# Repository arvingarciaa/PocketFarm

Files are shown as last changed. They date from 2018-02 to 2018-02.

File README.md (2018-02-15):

# PocketFarm

## Abstract

PocketFarm aims to implement precision agriculture on a farm using a network of sensors and data from online weather sources. Low cost and efﬁcient sensors and microcontroller will be used to make an effective farm monitoring system to help the farmer monitor the irrigation. An efﬁcient irrigation system correlates to low cost farming and high yield of crops.

The project is based on a Philippine setting and may include Asia/Philippine-based stores and references.

## Use Case

Since this project is centered around ease of use and convenience, PocketFarm enables a semi-automatic irrigation system through text messaging, weather forecasts, and on-farm sensors. The farmer will have an electronic system integrated directly to their preferred mode of irrigation. Currently, we assume a [gravity irrigation system](https://www.youtube.com/watch?v=6-emq0cxhtU). 



---

## Project Components

### The Farm

To describe some the electronic components, a modified architectural diagram is presented as follows.



To clarify, the electronic system's brain is an [Arduino Uno (clone)](https://www.lazada.com.ph/arduino-uno-r3-arduino-compatible-board-with-usb-13329964.html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), where two sensors--[Capacitive Soil Moisture Sensor](https://www.dfrobot.com/wiki/index.php/Capacitive_Soil_Moisture_Sensor_SKU:SEN0193), and a [DHT22 Temperature and Humidity Module](https://www.dfrobot.com/wiki/index.php/DHT22_Temperature_and_humidity_module_SKU:SEN0137)-- are connected, along with a [solenoid valve](https://www.makerlab-electronics.com/product/plastic-water-solenoid-valve-12v-1-2-nps/) which will control the irrigation system. In addition, a [GSM module](https://www.elecrow.com/sim800c-gprs-gsm-shield-for-arduino.html) serves as the communications link to the central remote server, which does all the processing and decisions.

### The Central Server

The central server is powered by a [Raspberry Pi](https://www.adafruit.com/product/998) hooked to the same [GSM module](https://www.elecrow.com/sim800c-gprs-gsm-shield-for-arduino.html) used in the farm setup. Additionally, the code is written in JavaScript, through Node.js to easily facilitate a front-end solution in the near future.

The server takes in all sensor data from all farm setups (soil moisture, temperature, and humidity), and their corresponding weather forecast data from [WeatherUnderground](https://www.wunderground.com). The server also facilitates scheduled farm irrigation, by sending commands to the farm setups.

---

## What's Inside

The repository contains the following directories.
```bash
./
|-- arduino/  
    # Contains all Arduino-related code, including previous revisions.
|-- server/  
    # Contains all server-related code, including previous revisions. They're meant to be run via Node.js.
|-- schematics/     
    # Contains all PCB schematics and layouts created for both the Raspberry Pi server setup and Arduino setup for the farm.
```

[1]: https://i.imgur.com/4u4o8eJ.png
[2]: https://i.imgur.com/9hq7tE3.png

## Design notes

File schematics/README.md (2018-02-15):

# PCB Fabrication at Home
This is a series of notes for me when I'm fabricating at home, so that I don't make the same mistakes next time. This was originally coming from PocketFarm-related experiences.

All of these are in a Philippine setting, and so will occasionally mention Philippine-based stores and retailers.

---

## Prerequisites
Most of the links here are from online stores, but they're usually _waaay_ cheaper when bought directly in-store (I think it's because the include the shipping costs with the product already, which isn't cost-effective when you're buying a lot from the same store; marketing tactics).
### Basic Stuff (buy and cut the board first!)
* a drill (_I use a Dremel 4000_)
* drill bits (_0.8mm, 1.0mm, 2.5mm, 3.0mm_)
* cut off wheel
* Presensitized PCB (_Kinsten, from e-Gizmo_)
* developer solution (_this came with the Presensitized PCB_)
### Layouting and UV Exposure
* Tracing Paper
* Laser Printer (_Inkjet apparently is equally fine, with a few quirks_)
* DIY UV exposure box (_Diploma Frame, a bunch of UV LEDs, a switch, a DC Jack_)
* Scissors
### Developing and Etching
* Muriatic Acid (_30% Hydrochloric Acid_)
* Hydrogen Peroxide (_Agua Oxigenada, larger volumes might be fine_)
* liquid containers (_I bought a 1L plastic container for the etching solution, and peanut butter jars for the developer solution_)
* two shallow containers for the developer solution and the etching solution
* face mask (_I use both a dust mask and earloop type mask from Mercury Drug_)
* safety goggles
* nitrile gloves (_I bought an industry-grade one for reusability_)
* glass funnel (_cannot emphasize how important this is_)
* nail polish (_acetone_)
* tissue paper (_lots_)
* absorbent cotton
### Placing and Soldering the Components
* soldering iron with a temperature knob (_mine came from China but [this](https://www.lazada.com.ph/adjustable-soldering-iron-60w-yihua-947-iii-8855270.html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) is basically it_)
* soldering [iron tip](https://www.makerlab-electronics.com/product/type-b-soldering-iron-tip/)
* solder (_Super Rubicon, 1 roll, 60%, 1.0m/m_)
* lead free tip tinner (_[Edsyn LT-1](https://www.lazada.com.ph/edsyn-lt-1-lead-free-soldering-tip-tinner-6777194.html), this is to revitalize the soldering tip_)
* blu-tack (_I'm using cheap transparent tape in the meantime._)
* desoldering pump or desoldering wick

---

## PCB Designing and Layouting
I'm using KiCad. I'm swearing by the Getting Started manual. Since I'm only doing single-sided designs, I always use the Back Layer. Here are my Design Rules for Pcbnew.



However, the clearance and the component vias are a bit small. I need to improve on this later.

Place some text on the Back Layer, and make sure it looks inverted. Print it on tracing paper (or transparency film) on a laser printer. When using an Inkjet Printer, make sure that the tracing paper doesn't jam, or curl during the process. Wet ink makes the tracing paper curl, and you may end up with an unusuable print. 

Make sure to inspect the print quality before proceeding.

## Exposing the Photoresist
Place the tracing paper where the printed side faces the PCB later on. You can check if this is the case by looking it through the ceiling, and you can read the text. Tape it into the glass frame, and once done (assuming that the board was already pre-cut), turn off the lights, peel the protective layer, and move quickly.

Place the PCB on the frame, aligned with the printout, lock the frame, and place it on the UV exposure box. Set the timer to 1 minute and 30 seconds, and turn on the lights. While this is happening, wear all protective equipment (goggles, mask, gloves).

## Developing the Exposed Board
The developer solution can be reused. Place caution into dissolving too much into the solution. The middle part of the PCB always develops last, and when this happens too slowly, add a little bit more of the developer powder. Adding too much developer powder will eat out photoresist on areas you don't intend to, and will lead to failure.

Inspect the board visually by rising it from time to time, and make sure you get everything covered (or erased).

## Etching and Exposing the Developed Board
I'm using Cupric Chloride as etchant. Some notes.
* Pure muriatic acid etches very, very quickly. It also produces a lot of fumes, noticeably making it a little bit harder to breathe.
* In the beginning, do a 1:1 ratio of HCl and H2O2.
* Add H2O2 when the solution begins to become olive green in color. Mix well.
* Add HCl when the copper isn't removed quickly. This is usually noticeable at the edges.
* Never add chemicals directly to the board. Do it on the side, then quickly agitate the solution.
* Cupric Chloride on Aqueous Hydrochloric Acid requires reoxidation. If this is done quite frequently, invest on an aquarium air pump (this will also do the agitation necessary for the board), or add H2O2 once in a while.
* CuCl stains. Make sure tissue is in standby nearby. I use a basin below the CuCl container to collect spilling etchant.
* If the recycled etchant doesn't work very well, start with a sizeable amount, then apply more HCl. This allows for a relatively faster etching process, without the excess fumes.
* When satisfied, remove the board from the etchant, dry it with tissue paper, and remove the photoresist with acetone (nail polish). You'd want to use this with cotton balls than tissue paper as cotton holds to the acetone for a little bit longer.
* When all copper components are exposed, clean the board (front and back with alcohol).
* Remember to follow your city guidelines on hazardous waste disposal. Never, ever, try to drain your chemicals directly down the sink!

## Drilling and Cutting the Etched Board
* Dremel 4000's speed works well set to 15--for cutting, drilling, and 5/10 for polishing.
* You'll get a lot of thin drill bits breaking easily, frequently. Make sure to have a lot of backup, and maybe invest on a Multi Chuck (Dremel 4486).
* I'm using a book as a vise/clamp. Invest in a better solution.
* Most through-hole components will work with 0.8mm, but 1.0mm breaks less frequently.
* Big holes are usually of the 3.0mm variant.
* DC jacks use a 2.5mm for the GND and the Switch, and a 3.0mm for the VCC.

## Soldering Through-Hole Components to the PCB
* Use blu-tack for temporarily fastening the components before soldering.
* Make sure to use a sharp tip rather than a tip with a flat end to make soldering jobs less ugly.

---
Take care!

[1]: https://i.imgur.com/gUOFxXU.png

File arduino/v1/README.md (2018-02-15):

# PocketFarm version 1 (Server)

## Setup

The setup for the first revision were as follows.

## The Farm

The farm setup was assigned a GSM number which serves as the main communication point of the farmer. It will react to messages with a specific code/format--get sensor data, get weather forecast, or get irrigation suggestions. To facilitate requests for weather forecasts or irrigiation suggestions, the farm unit will forward the request to the central server, in which it will reply back with the requested resource.

A [GSM shield](https://www.elecrow.com/sim800c-gprs-gsm-shield-for-arduino.html) is attached to the Arduino, with the [Capacitive Soil Moisture Sensor](https://www.dfrobot.com/wiki/index.php/Capacitive_Soil_Moisture_Sensor_SKU:SEN0193) connected to `A5`, and the [DHT22 Temperature and Humidity Module](https://www.dfrobot.com/wiki/index.php/DHT22_Temperature_and_humidity_module_SKU:SEN0137) connected to `A0`.

The code is available at `/arduino/v1/final_working/final_working.ino`.

## The Central Server
The central server relied on an Arduino with a GSM shield to receive texts from the farm units, and a Node.js server to facilitate processing. They are both communicating via WebSockets, and so requires the Arduino connected to both a [GSM shield](https://www.elecrow.com/sim800c-gprs-gsm-shield-for-arduino.html) and an [Ethernet shield](http://www.elecrow.com/w5100-ethernet-shield-for-arduino-p-670.html). 

While this setup offers flexibility (i.e., the Arduino setup can be running 24/7 somewhere connected to a router, and the server can be hosted offshore to ensure reliability), it poses issues on cost, redundancy, and speed.

The Arduino code is available at `/arduino/v1/WebSocketGSMBridge`.
The server code is available at `/server/v1`. It can be run using `npm start`. Make sure to duplicate `/server/v1/example.env` to `/server/v1/.env` and add your keys before running.

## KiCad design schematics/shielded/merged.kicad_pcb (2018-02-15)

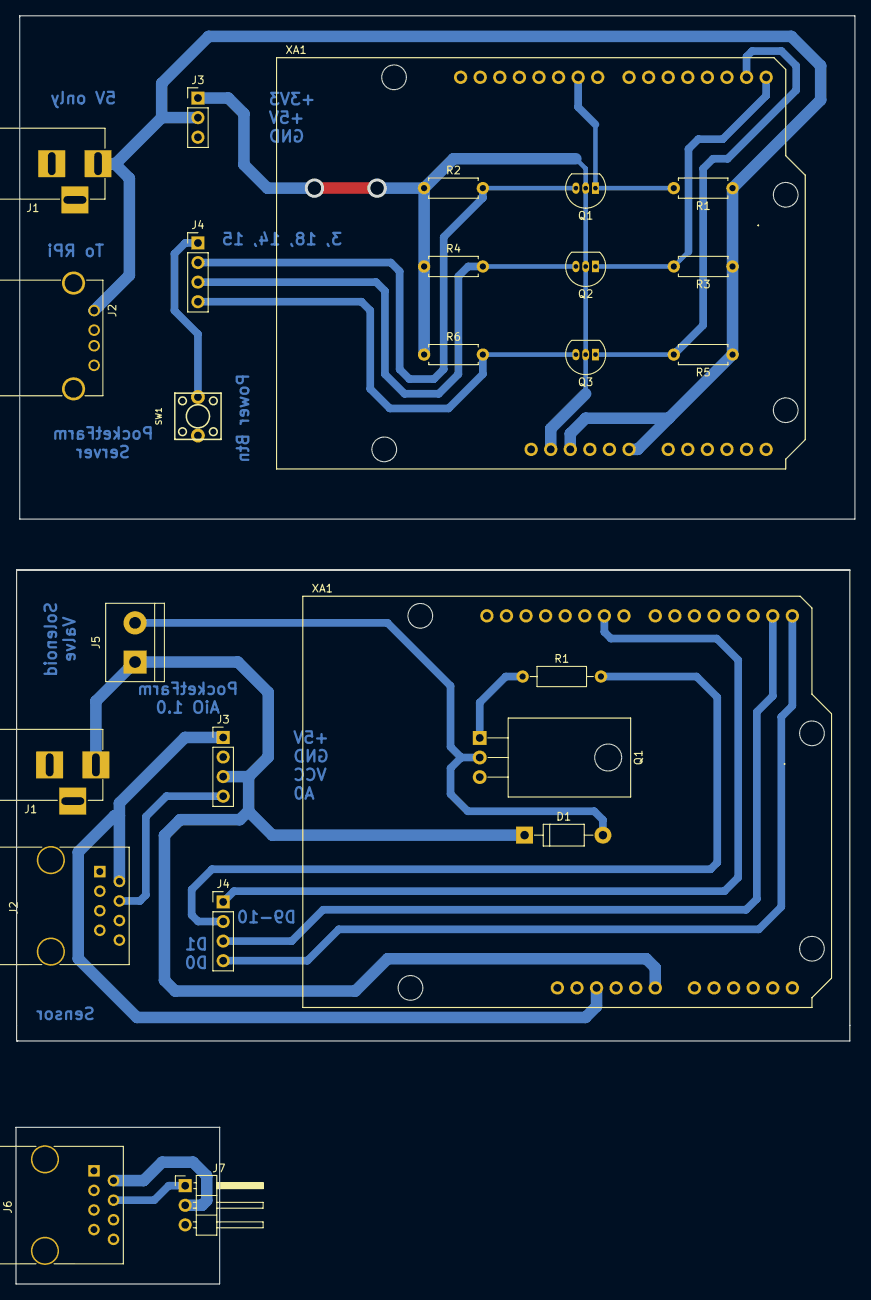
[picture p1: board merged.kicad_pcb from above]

Board: 2 copper layers, 108.8 x 164.5 mm, 26 parts (0 on the bottom side), 37 nets.

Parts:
D1: 1N4001; D_DO-41_SOD81_P10.16mm_Horizontal
J1, J1#2: Jack-DC; BARREL_JACK
J2: USB_A
J2#2: RJ45_BUILTIN; RJ45_8
J3: Conn_01x03_Male; Pin_Header_Straight_1x03_Pitch2.54mm
J3#2, J4, J4#2: Conn_01x04_Male; Pin_Header_Straight_1x04_Pitch2.54mm
J5: Screw_Terminal_01x02; TerminalBlock_bornier-2_P5.08mm
J6: RJ45_SENSOR; RJ45_8
J7: Conn_01x03_Male; Pin_Header_Angled_1x03_Pitch2.54mm
Q1, Q2, Q3: 2N7000; TO-92_Inline_Narrow_Oval
Q1#2: TIP120; TO-220-3_Horizontal
R1, R2, R3, R4, R5, R6: 10k; R_Axial_DIN0207_L6.3mm_D2.5mm_P7.62mm_Horizontal
R1#2: 1k; R_Axial_DIN0207_L6.3mm_D2.5mm_P10.16mm_Horizontal
SW1: SW_SPST; SPST-2-PIN_6mm_thru
XA1, XA1#2: Arduino_Uno_Shield

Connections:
+3V3: J3.1, Q1.2, Q2.2, Q3.2, R2.1, R4.1, R6.1, XA1.3.3V
+5V: J1.1, J2.1, J2#2.2, J3.2, J3#2.1, J6.2, J7.2, R1.1, R3.1, R5.1, XA1.5V1, XA1.VIN, XA1#2.5V1
/A0: J2#2.4, J3#2.4, J6.4, J7.1
/D0_TX1: J4#2.4, XA1#2.D0
/D1_RX1: J4#2.3, XA1#2.D1
/D9: J4#2.1, XA1#2.D9
/D10: J4#2.2, R1#2.2
/GPIO3: J4.1, SW1.1
/GPIO18: J4.2, Q1.3, R2.2
/RXD0_15: J4.4, Q3.3, R6.2
/TXD0_14: J4.3, Q2.3, R4.2
GND: J1.2, J1#2.2, J2.4, J2#2.1, J2#2.3, J2#2.5, J2#2.6, J2#2.7, J2#2.8, J3.3, J3#2.2, J6.1, J6.3, J6.5, J6.6, J6.7, J6.8, J7.3, Q1#2.3, SW1.2, XA1.GND1, XA1.GND2, XA1.GND3, XA1#2.GND1, XA1#2.GND2, XA1#2.GND3
unnamed: D1.2, J5.2, Q1#2.2
unnamed: J1.3, J1#2.3
unnamed: Q1.1, Q1#2.1, R1.2, R1#2.1, XA1.D9
unnamed: Q2.1, R3.2, XA1.D0
unnamed: Q3.1, R5.2, XA1.D1
unnamed: XA1.A0, XA1#2.A0
unnamed: XA1.A1, XA1#2.A1
unnamed: XA1.A2, XA1#2.A2
unnamed: XA1.A3, XA1#2.A3
unnamed: XA1.A4, XA1#2.A4
unnamed: XA1.A5, XA1#2.A5
unnamed: XA1.AREF, XA1#2.AREF
unnamed: XA1.D2, XA1#2.D2
unnamed: XA1.D3, XA1#2.D3
unnamed: XA1.D4, XA1#2.D4
unnamed: XA1.D5, XA1#2.D5
unnamed: XA1.D6, XA1#2.D6
unnamed: XA1.D7, XA1#2.D7
unnamed: XA1.D8, XA1#2.D8
unnamed: XA1.D10, XA1#2.D10
unnamed: XA1.D11, XA1#2.D11
unnamed: XA1.D12, XA1#2.D12
unnamed: XA1.D13, XA1#2.D13
unnamed: XA1.RST1, XA1#2.RST1
VCC: D1.1, J1#2.1, J3#2.3, J5.1, XA1#2.VIN

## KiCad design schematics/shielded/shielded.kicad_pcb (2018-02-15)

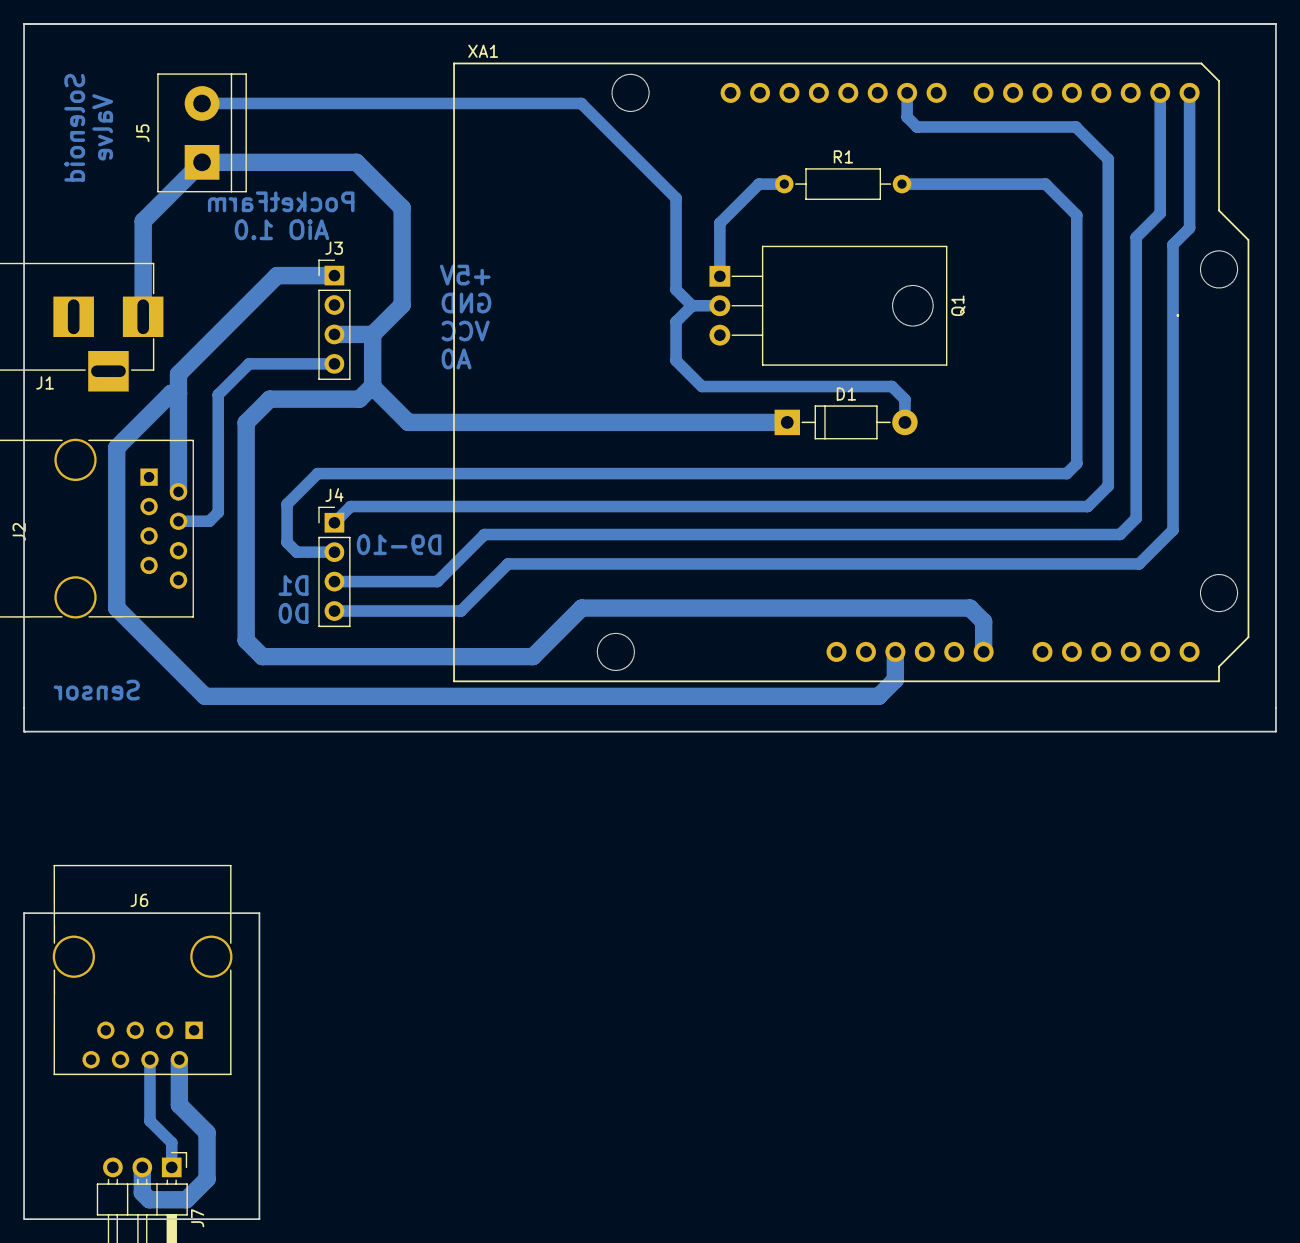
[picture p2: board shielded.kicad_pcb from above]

Board: 2 copper layers, 108.1 x 61.1 mm, 11 parts (0 on the bottom side), 10 nets.

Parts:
D1: 1N4001; D_DO-41_SOD81_P10.16mm_Horizontal
J1: Jack-DC; BARREL_JACK
J2: RJ45_BUILTIN; RJ45_8
J3, J4: Conn_01x04_Male; Pin_Header_Straight_1x04_Pitch2.54mm
J5: Screw_Terminal_01x02; TerminalBlock_bornier-2_P5.08mm
J6: RJ45_SENSOR; RJ45_8
J7: Conn_01x03_Male; Pin_Header_Angled_1x03_Pitch2.54mm
Q1: TIP120; TO-220-3_Horizontal
R1: 1k; R_Axial_DIN0207_L6.3mm_D2.5mm_P10.16mm_Horizontal
XA1: Arduino_Uno_Shield

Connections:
+5V: J2.2, J3.1, J6.2, J7.2, XA1.5V1
/A0: J2.4, J3.4, J6.4, J7.1
/D0_TX1: J4.4, XA1.D0
/D1_RX1: J4.3, XA1.D1
/D9: J4.1, XA1.D9
/D10: J4.2, R1.2
GND: J1.2, J2.1, J2.3, J2.5, J2.6, J2.7, J2.8, J3.2, J6.1, J6.3, J6.5, J6.6, J6.7, J6.8, J7.3, Q1.3, XA1.GND1, XA1.GND2, XA1.GND3
unnamed: D1.2, J5.2, Q1.2
unnamed: Q1.1, R1.1
VCC: D1.1, J1.1, J3.3, J5.1, XA1.VIN

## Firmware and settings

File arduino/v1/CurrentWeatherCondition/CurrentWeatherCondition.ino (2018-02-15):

/****************************
The MIT License (MIT)
Copyright (c) 2015 by bbx10node@gmail.com
Permission is hereby granted, free of charge, to any person obtaining a copy
of this software and associated documentation files (the "Software"), to deal
in the Software without restriction, including without limitation the rights
to use, copy, modify, merge, publish, distribute, sublicense, and/or sell
copies of the Software, and to permit persons to whom the Software is
furnished to do so, subject to the following conditions:
The above copyright notice and this permission notice shall be included in all
copies or substantial portions of the Software.
THE SOFTWARE IS PROVIDED "AS IS", WITHOUT WARRANTY OF ANY KIND, EXPRESS OR
IMPLIED, INCLUDING BUT NOT LIMITED TO THE WARRANTIES OF MERCHANTABILITY,
FITNESS FOR A PARTICULAR PURPOSE AND NONINFRINGEMENT. IN NO EVENT SHALL THE
AUTHORS OR COPYRIGHT HOLDERS BE LIABLE FOR ANY CLAIM, DAMAGES OR OTHER
LIABILITY, WHETHER IN AN ACTION OF CONTRACT, TORT OR OTHERWISE, ARISING FROM,
OUT OF OR IN CONNECTION WITH THE SOFTWARE OR THE USE OR OTHER DEALINGS IN THE
SOFTWARE.
******************************/

#ifndef min
#define min(x,y) (((x)<(y))?(x):(y))
#endif
#ifndef max
#define max(x,y) (((x)>(y))?(x):(y))
#endif
#include <ArduinoJson.h>
#include <SPI.h>
#include <Ethernet.h>



// Use your own API key by signing up for a free developer account.
// http://www.wunderground.com/weather/api/
#define WU_API_KEY "YOUR_KEY"

// Specify your favorite location one of these ways.
//#define WU_LOCATION "CA/HOLLYWOOD"

// US ZIP code
//#define WU_LOCATION ""
#define WU_LOCATION "90210"

// Country and city
//#define WU_LOCATION "Australia/Sydney"

// 5 minutes between update checks. The free developer account has a limit
// on the  number of calls so don't go wild.
#define DELAY_NORMAL    (5*60*1000)
// 20 minute delay between updates after an error
#define DELAY_ERROR     (20*60*1000)

#define WUNDERGROUND "api.wunderground.com"

// HTTP request
const char WUNDERGROUND_REQ[] =
    "GET /api/YOUR_KEY/conditions/pws:1/q/pws:ICALABAR18.json HTTP/1.1\r\n"
    "Host: api.wunderground.com\r\n"
    "Connection: close\r\n"
    "\r\n";

void setup()
{
  Serial.begin(9600);

  // We start by connecting to a WiFi network
  Serial.println();
  Serial.println();
  while (!Serial) {
    ;  // wait for serial port to initialize
  }
  Serial.println("Serial ready");

  byte mac[] = {0xDE, 0xAD, 0xBE, 0xEF, 0xFE, 0xED};
  if (!Ethernet.begin(mac)) {
    Serial.println("Failed to configure Ethernet");
    return;
  }
  Serial.println("Ethernet ready");
  delay(1000);

  Serial.println();
}

static char respBuf[4096];

void loop()
{
  // TODO check for disconnect from AP

  // Open socket to WU server port 80
  Serial.print(F("Connecting to "));
  Serial.println(WUNDERGROUND);

  // Use WiFiClient class to create TCP connections
  EthernetClient client;
  const int httpPort = 80;
  if (!client.connect(WUNDERGROUND, httpPort)) {
    Serial.println(F("connection failed")); 
    delay(DELAY_ERROR);
    return;
  }

  // This will send the http request to the server
  Serial.print(WUNDERGROUND_REQ);
  client.print(WUNDERGROUND_REQ);
  client.flush();

  // Collect http response headers and content from Weather Underground
  // HTTP headers are discarded.
  // The content is formatted in JSON and is left in respBuf.
  int respLen = 0;
  bool skip_headers = true;
  while (client.connected() || client.available()) {
    if (skip_headers) {
      String aLine = client.readStringUntil('\n');
      //Serial.println(aLine);
      // Blank line denotes end of headers
      if (aLine.length() <= 1) {
        skip_headers = false;
      }
    }
    else {
      int bytesIn;
      bytesIn = client.read((uint8_t *)&respBuf[respLen], sizeof(respBuf) - respLen);
      Serial.print(F("bytesIn ")); Serial.println(bytesIn);
      if (bytesIn > 0) {
        respLen += bytesIn;
        if (respLen > sizeof(respBuf)) respLen = sizeof(respBuf);
      }
      else if (bytesIn < 0) {
       Serial.print(F("read error "));
       Serial.println(bytesIn);
      }
    }
    delay(1);
  }
  client.stop();
  if (respLen >= sizeof(respBuf)) {
    Serial.print(F("respBuf overflow "));
    Serial.println(respLen);
    delay(DELAY_ERROR);
    return;
  }
  // Terminate the C string
  respBuf[respLen++] = '\0';
  Serial.print(F("respLen "));
  Serial.println(respLen);
  //Serial.println(respBuf);

  if (showWeather(respBuf)) {
    delay(DELAY_NORMAL);
  }
  else {
    delay(DELAY_ERROR);
  }
}

bool showWeather(char *json)
{
  StaticJsonBuffer<3*1024> jsonBuffer;

  // Skip characters until first '{' found
  // Ignore chunked length, if present
  char *jsonstart = strchr(json, '{');
  //Serial.print(F("jsonstart ")); Serial.println(jsonstart);
  if (jsonstart == NULL) {
    Serial.println(F("JSON data missing"));
    return false;
  }
  json = jsonstart;

  // Parse JSON
  //Serial.println(json);
  JsonObject& root = jsonBuffer.parseObject(json);
  if (!root.success()) {
    Serial.println(F("jsonBuffer.parseObject() failed"));
    return false;
  }

  // Extract weather info from parsed JSON

  JsonObject& current = root["current_observation"];
  const float temp_f = current["temp_f"];
  Serial.print(temp_f, 1); Serial.print(F(" F, "));
  const float temp_c = current["temp_c"];
  Serial.print(temp_c, 1); Serial.print(F(" C, "));
  const char *humi = current[F("relative_humidity")];
  Serial.print(humi);   Serial.println(F(" RH"));
  const char *weather = current["weather"];
  Serial.println(weather);
  const char *pressure_mb = current["pressure_mb"];
  Serial.println(pressure_mb);
  const char *observation_time = current["observation_time_rfc822"];
  Serial.println(observation_time);

  const char *location = current["observation_location"]["full"];
  Serial.println(location);
//char day[128]; 
/*
Serial.println();
Serial.println();
JsonObject& current = root["forecast"];
Serial.print("Weather forecast for ");
const char *day = root["forecast"]["txt_forecast"]["forecastday"][2]["title"];
//strcpy(day, root["forecast"]["txt_forecast"]["forecastday"][2]["title"]);
Serial.print(day);
Serial.println(": ");
*/
/*
  // Extract local timezone fields
  const char *local_tz_short = current["local_tz_short"];
  Serial.println(local_tz_short);
  const char *local_tz_long = current["local_tz_long"];
  Serial.println(local_tz_long);
  const char *local_tz_offset = current["local_tz_offset"];
  Serial.println(local_tz_offset);

  */
  return true;
}

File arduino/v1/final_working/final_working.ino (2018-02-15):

// send SMS "on", if will turn on the LED
// send SMS "off", if will turn off the LED
#include <SoftwareSerial.h>
#include <DHT.h>;

//Constants
SoftwareSerial mySerial(7, 8);
#define DHTPIN A5     // what pin we're connected to
#define DHTTYPE DHT22   // DHT 22  (AM2302)
DHT dht(DHTPIN, DHTTYPE); //// Initialize DHT sensor for normal 16mhz Arduino
#define myTime (1000UL * 20 * 1) // timeer (milli * secs * mins)
unsigned long rolltime = millis() + myTime;


//Global Variables
String msg = String("");
int SmsContentFlag = 0;
int ledPin = 13;
int menuFlag = 0;
int subFlag = 0;
int forecastSubsFlag = 0;
int moistureSensor = A0;
int subCounter = 0;
String destNo = String("");
String subNo = String("");
int chk;
float hum;  //Stores humidity value
float temp; //Stores temperature value


void setup()
{
  mySerial.begin(19200);               // the GPRS baud rate   
  Serial.begin(19200);                 // the GPRS baud rate
  
  pinMode( ledPin, OUTPUT ); 
  digitalWrite( ledPin, LOW ); 
  mySerial.println("\r");
  mySerial.println( "AT+CMGF=1" );
}
 
void loop()
{
    char SerialInByte;
    if((long)(millis() - rolltime) >= 0) {
       if(forecastSubsFlag==1){
        subCounter++;
        mySerial.print("AT+CMGS=");
        mySerial.print(subNo);
        mySerial.print("\r"); 
        delay(100);
        mySerial.print("Subscription Message #");   //The text for the message
        mySerial.print(subCounter);
        delay(100);
        mySerial.write(0x1A);  //Equivalent to sending Ctrl+Z 
      }
      rolltime += myTime;
    }    
    if(Serial.available())
    {
       mySerial.print((unsigned char)Serial.read());
    }  
    else if(mySerial.available())
    {
        char SerialInByte;
        SerialInByte = (unsigned char)mySerial.read();
        Serial.print( SerialInByte );
        if( SerialInByte == 13 )
        {
          ProcessGprsMsg();
         }
         if( SerialInByte == 10 ){
            // EN: Skip Line feed
         }
         else {
           // EN: store the current character in the message string buffer
           msg += String(SerialInByte);
         }
     }   
}
 
// EN: Make action based on the content of the SMS. 
//     Notice than SMS content is the result of the processing of several GPRS shield messages.

void ProcessSms( String sms )
{
  Serial.print( "ProcessSms for [" );
  Serial.print( sms );
  Serial.println( "]" );
  sms.toLowerCase();
  
  
  //mySerial.print("AT+CMGS=\"+639278378105\"\r");    //Start accepting the text for the message
  //delay(100);
  mySerial.print("AT+CMGS=");
  mySerial.print(destNo);
  mySerial.print("\r"); 
  delay(100);
  if( sms.indexOf("menu") >= 0){
    if(subFlag%2==0){
       mySerial.print("Choose an option \r[1] Subscribe to daily forecasts \r[2] Fetch soil moisture content\r[3] Fetch humidity and temperature \r[4] Subscribe to irrigation suggestions \r\rSend to this number, e.g. \"1\"");   //The text for the message
    } else {
       mySerial.print("Choose an option \r[1] Unubscribe to daily forecasts \r[2] Fetch soil moisture content\r[3] Fetch humidity and temperature \r[4] Subscribe to irrigation suggestions \r\rSend to this number, e.g. \"1\"");   //The text for the message
    }
    delay(100);
    mySerial.write(0x1A);  //Equivalent to sending Ctrl+Z 
    return;
  }
  if( sms.indexOf("1") >= 0){ //Subscribe to daily forecasts
    if(subFlag%2==0){
       subFlag++;
       subNo = destNo;
       forecastSubsFlag = 1;
       mySerial.print("Subscribed to daily forecast!");   //The text for the message   
    } else {
       subFlag++;
       forecastSubsFlag = 0;
       subCounter = 0;
       mySerial.print("Unsubscribed to daily forecast!");   //The text for the message   
    }
    delay(100);
    mySerial.write(0x1A);
    menuFlag = 0;
    return; 
  }
  if( sms.indexOf("2") >= 0){ //Subscribe to daily forecasts
    mySerial.print("15% per cubic meter");   //The text for the message
    delay(100);
    mySerial.write(0x1A);
    return; 
  }
  if( sms.indexOf("3") >= 0){ //Subscribe to daily forecasts
    hum = dht.readHumidity();
    temp= dht.readTemperature();
    //Print temp and humidity values to serial monitor
    mySerial.print("Humidity: ");
    mySerial.print(hum);
    mySerial.print(" %, Temp: ");
    mySerial.print(temp);
    mySerial.print(" Celsius");
    delay(100);
    mySerial.write(0x1A);
    return; 
  }
  //mySerial.println( "AT+CMGD=1,4" );
  mySerial.print("Invalid Code");
  delay(100);
  mySerial.write(0x1A);
  return;
}

// EN: Request Text Mode for SMS messaging


 
void GprsReadSmsStore( String SmsStorePos ){
  mySerial.print( "AT+CMGR=" );
  mySerial.println( SmsStorePos );
}
 
// EN: Clear the GPRS shield message buffer

void ClearGprsMsg(){
  msg = "";
}
 
// EN: interpret the GPRS shield message and act appropiately

void ProcessGprsMsg() 
{
    Serial.println("");
    Serial.print( "GPRS Message: [" );
    Serial.print( msg );
    Serial.println( "]" );
    if( msg.indexOf( "Call Ready" ) >= 0 )
   {
       Serial.println( "*** GPRS Shield registered on Mobile Network ***" );
       mySerial.println( "AT+CMGF=1" );
   }
 
  // EN: unsolicited message received when getting a SMS message
  // FR: Message non sollicité quand un SMS arrive
  if( msg.indexOf( "+CMTI" ) >= 0 )
  {
     Serial.println( "*** SMS Received ***" );
     // EN: Look for the coma in the full message (+CMTI: "SM",6)
     //     In the sample, the SMS is stored at position 6
     int iPos = msg.indexOf( "," );
     String SmsStorePos = msg.substring( iPos+1 );
     Serial.print( "SMS stored at " );
     Serial.println( SmsStorePos );
 
     // EN: Ask to read the SMS store
     GprsReadSmsStore( SmsStorePos );
  }
 
  // EN: SMS store readed through UART (result of GprsReadSmsStore request)  
  if( msg.indexOf( "+CMGR:" ) >= 0 )
  {
    Serial.println("====================");
    Serial.print("Source phone number is: ");
    //gets the sender's phone number
    destNo = "";
    for(int i=22; i<35; i++){
      destNo = destNo + msg[i];
    }
    destNo = "\"" + destNo + "\"";
    Serial.println(destNo);
    Serial.println(destNo.length());
    Serial.println("====================");
    // EN: Next message will contains the BODY of SMS
    if(destNo.length()==15){
      SmsContentFlag = 0;
    }
    SmsContentFlag = 1;
   
    // EN: Following lines are essentiel to not clear the flag!
    ClearGprsMsg();
    return;
  }
 
  // EN: +CMGR message just before indicate that the following GRPS Shield message 
  //     (this message) will contains the SMS body

  if( SmsContentFlag == 1 )
  {
    Serial.println( "*** SMS MESSAGE CONTENT ***" );
    Serial.println( msg );
    Serial.println( "*** END OF SMS MESSAGE ***" );
    ProcessSms( msg );
  }

  ClearGprsMsg();
 // mySerial.println( "AT+CMGD=1,4" );
  // EN: Always clear the flag
  SmsContentFlag = 0; 
}

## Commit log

2018-02-15 Add server code as well
    [arduino_breakout.sch, merged.kicad_pcb, merged.sch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]
2018-02-15 Relocate previous code to /arduino/v1/
